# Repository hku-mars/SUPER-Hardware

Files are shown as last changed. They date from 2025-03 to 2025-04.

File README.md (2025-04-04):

# SUPER-Hardware

This repository contains the hardware components of the SUPER project. See the software part of SUPER at [hku-mars/SUPER (github.com)](https://github.com/hku-mars/SUPER)

If the following resources is useful to you, please cite our paper with

```bibtex
@article{ren2025safety,
  title={Safety-assured high-speed navigation for MAVs},
  author={Ren, Yunfan and Zhu, Fangcheng and Lu, Guozheng and Cai, Yixi and Yin, Longji and Kong, Fanze and Lin, Jiarong and Chen, Nan and Zhang, Fu},
  journal={Science Robotics},
  volume={10},
  number={98},
  pages={eado6187},
  year={2025},
  publisher={American Association for the Advancement of Science}
}
```

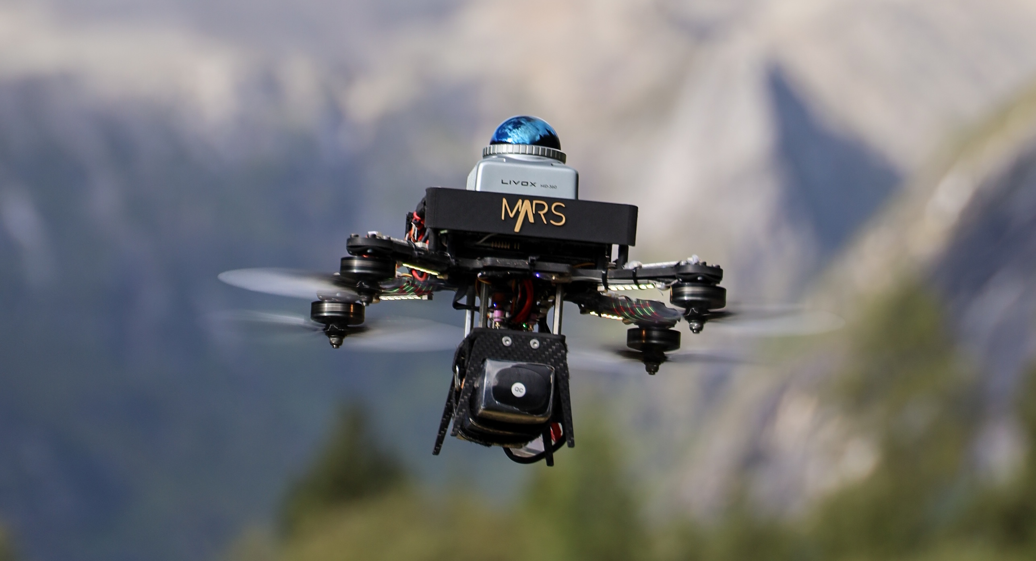
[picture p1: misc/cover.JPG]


## Provided Materials

We provide the following resources:

* Editable drafts and assemblies in SolidWorks: [./SolidWorks](./SolidWorks)
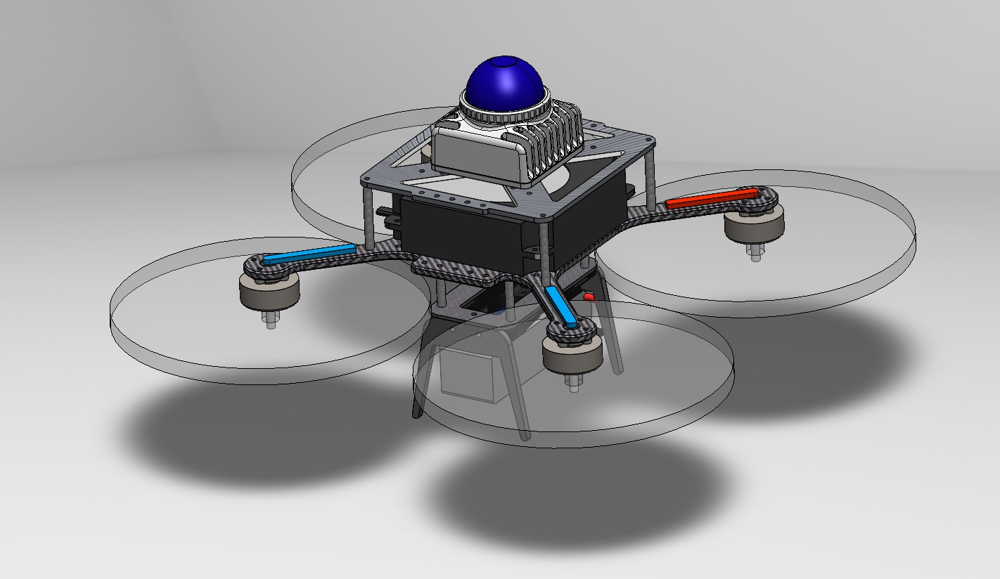
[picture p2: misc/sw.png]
  * 

* `.step` files for 3D printing: [./3DPrinting](./3DPrinting)

* `.step` files for carbon fiber cutting and engraving: [./CarbonFiber](./CarbonFiber)

Bill of Materials (BOM) for additional components with reference links (see table below)

## Hardware Breakdown

The hardware structure is illustrated below:

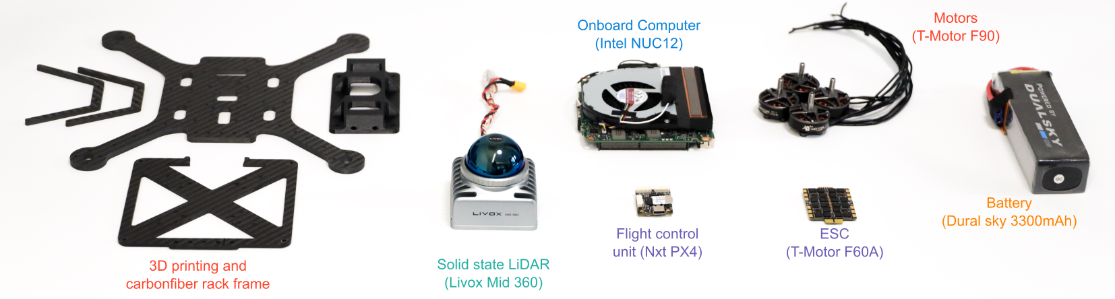
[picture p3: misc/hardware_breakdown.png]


## BOM

| Name | Type | Number | Reference Link |
| --- | --- | --- | --- |
| LiDAR | Livox MID360 | 1 | [Livox Mid-360 (livoxtech.com)](https://www.livoxtech.com/mid-360) |
| LiDAR Connecting Cable | N/A | 1 | [无名创新 Livox M12航插一分二数据线 mid360数据线 电赛无人机-淘宝网 (taobao.com)](https://item.taobao.com/item.htm?id=841090466365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{"aplus_abtest"%3A"eb7d480f961652917f78181296850d29"}&xxc=taobaoSearch) |
| Onboard Computer | Intel NUC | 1 | [ASUS NUC 12 Pro｜NUCs｜ASUS Global](https://www.asus.com/displays-desktops/nucs/nuc-kits/asus-nuc-12-pro/) |
| Aluminum Standoffs Pillars | 40 mm * 3 mm | 4 | |
| Aluminum Standoffs Pillars | 30 mm * 3 mm | 4 | (Or 8 pcs 40 mm * 3mm) |
| Motor | T-Motor F90 KV1300 | 4 | [T-MOTORHOBBY F90 2806.5 Long Range Motor - 1300KV/1500KV/1950KV_Motor_F Series Racing Power_FPV Drone Parts_Tmotorhobby Store-Tmotorobby drone motor,ESC,Propeller](https://tmotorhobby.com/goods.php?id=1057) |
| Propeller | HQ 7x4x3 | 4 | [HQProp 7X4X3 Light Grey](https://www.hqprop.com/hq-durable-prop-7x4x3-light-grey-2cw2ccw-poly-carbonate-popo-p0133.html)|
| ESC | T-Motor F60A mini 4 in 1 | 1 | [TMOTOR F60A MINI 20x20 4IN1 ESC for FPV Drones – T-Motor](https://shop.tmotor.com/products/f60a-mini-20x20-4in1-esc) |
| Battery | DualSky 3300mAh 6S XP-3300HED | 1 | [cn.dualsky.com/Xpower_LiPos/decc7a90-6c8f-5c0d-d0d4-c8eaced6f5d2.shtml](http://cn.dualsky.com/Xpower_LiPos/decc7a90-6c8f-5c0d-d0d4-c8eaced6f5d2.shtml) |
| Flight Controller | NxtPx4 | 1 | [NxtPX4v2(micoair.cn)](https://micoair.cn/docs/NxtPX4v2-fei-kong-yong-hu-shou-ce) |
| RC | Radiolink AT9S | 1 | [AT9S PRO 12 channels transmitter for racing drone, fixed wing, helicopter, glider, cars and boats (radiolink.com.cn)](https://www.radiolink.com.cn/at9spro) |
| Reveiver | Radiolink R12DSM | 1 | [12 channels MINI receiver R12DSM (radiolink.com)](https://www.radiolink.com/r12dsm) |
| Power Module | CKCS CK2416 (12 V 16 A)  | 1 | [https://e.tb.cn/h.6U3o07BuE81jHGi?tk=fopteCChcyW](https://e.tb.cn/h.6U3o07BuE81jHGi?tk=fopteCChcyW) |
### Notes:

- **RC and Receiver**: The listed models (Radiolink AT9S and R12DSM) are what we currently use, but alternatives are acceptable.

- **Battery**: Any 6S battery can be used, not necessarily the DualSky model listed.

- **Flight Controller**: Any PX4-compatible flight controller can substitute for the NxtPx4, as the MPC controller may be open-sourced later this year, and our development is based on PX4.

- **Power module for NUC**: We are currently using a customized DC-DC buck converter designed by a labmate, but we do not have plans to make it open-source at this time. However, you may find the following open-source option useful: [NUC Battery Power - Open Source Hardware Platform.](https://oshwhub.com/PancLAN/buck_for_nuc). Please note that this open-source solution is not very stable, which is why we are making some modifications. However, these updates are not being handled by me, so I don't have further details. We may provide updates in the future.

  **UPDATE 24/04/04:** I have found an alternative for NUC 13 or other types that supports 12 v inputs, listed in the table above.

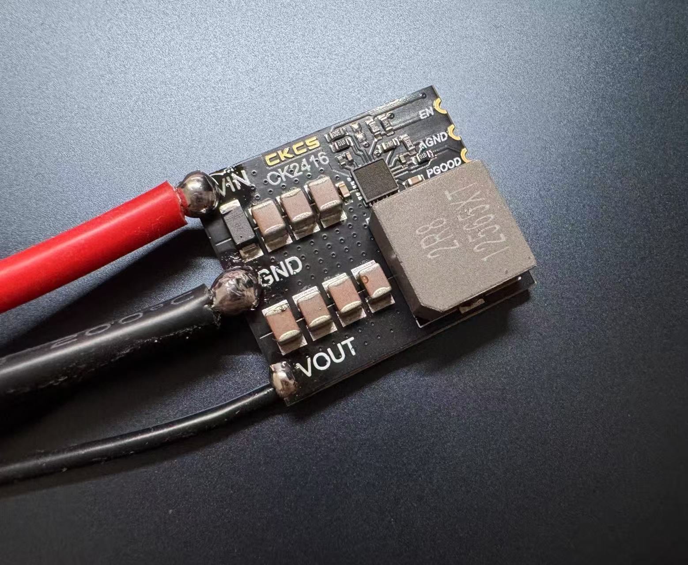
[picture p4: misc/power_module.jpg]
  

## Acknowledgments

- Special thanks to [NxtPx4](https://github.com/HKUST-Aerial-Robotics/Nxt-FC) for providing an excellent mini flight controller.
- Gratitude to all contributors: **Wenyi Liu**, **Wendi Dong**, **Minghe Chen**, and **Rongpei Dai**.

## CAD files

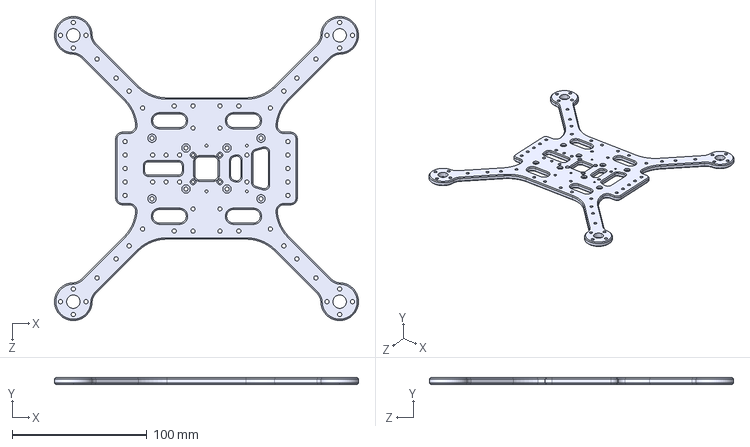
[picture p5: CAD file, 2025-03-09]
CarbonFiber/5mm_main_board.STEP
226.0 x 5.00 x 226.0 mm

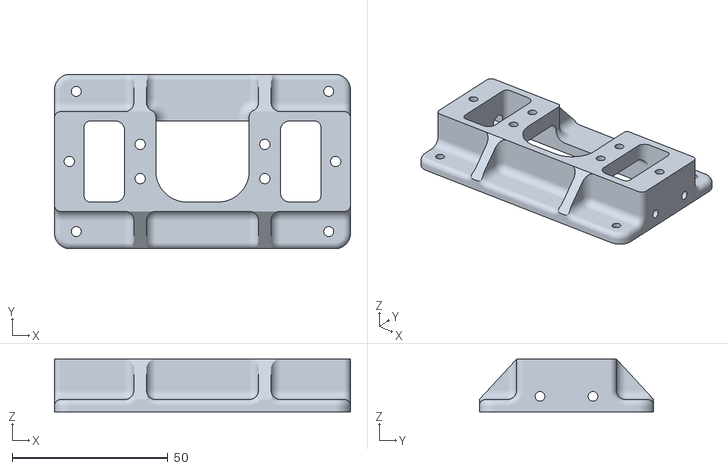
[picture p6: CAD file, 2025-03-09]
3DPriting/battery_board.stl
95.0 x 56.0 x 17.0

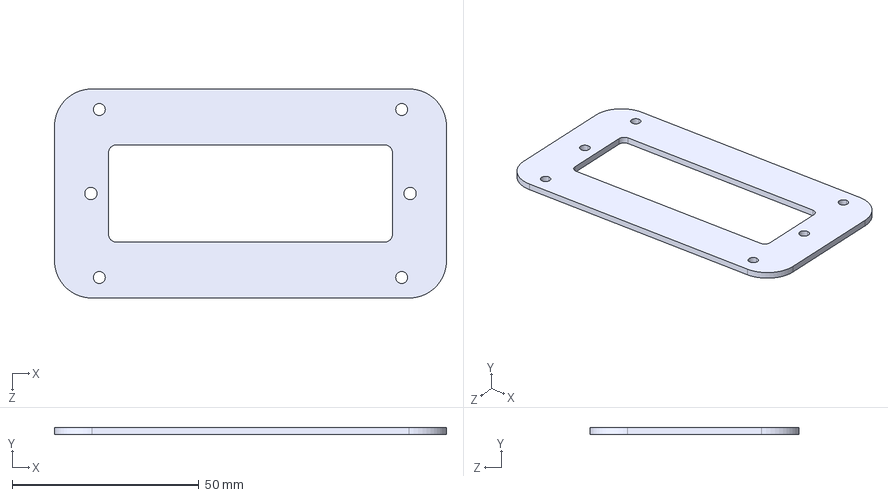
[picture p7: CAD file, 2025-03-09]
CarbonFiber/3mm_bat_board.step
105.0 x 2.00 x 56.0 mm

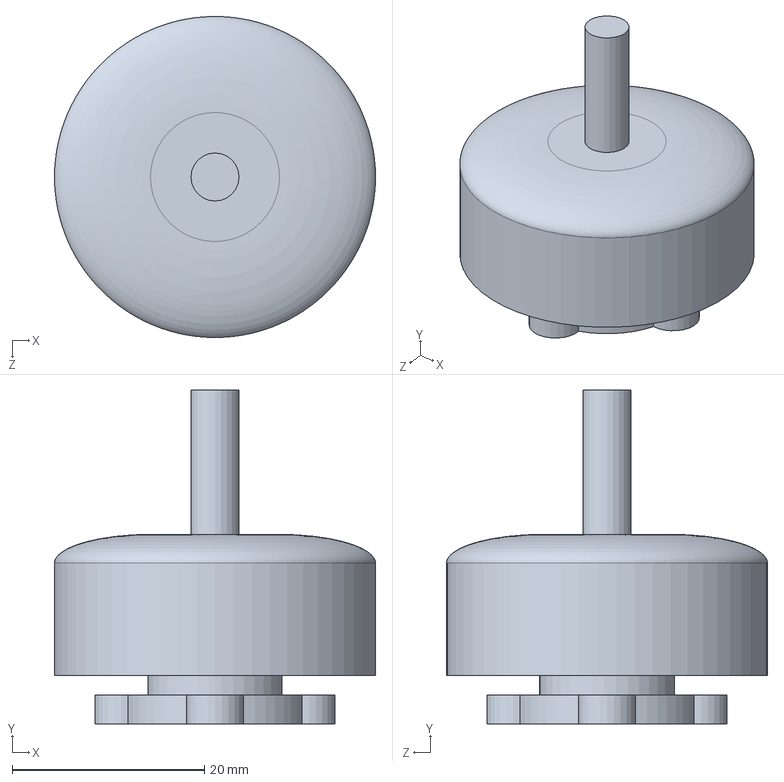
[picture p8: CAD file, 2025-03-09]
SolidWorks/yunque-F90_motor.SLDPRT
33.4 x 34.7 x 33.4 mm

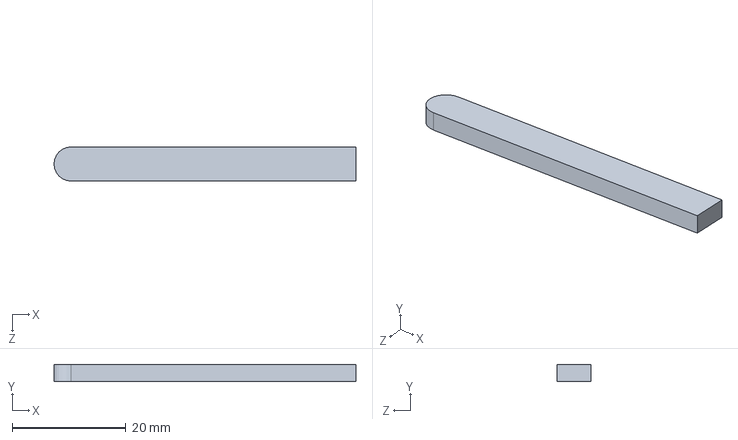
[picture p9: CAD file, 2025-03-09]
SolidWorks/yunque-led-b.SLDPRT
53.0 x 3.00 x 6.00 mm

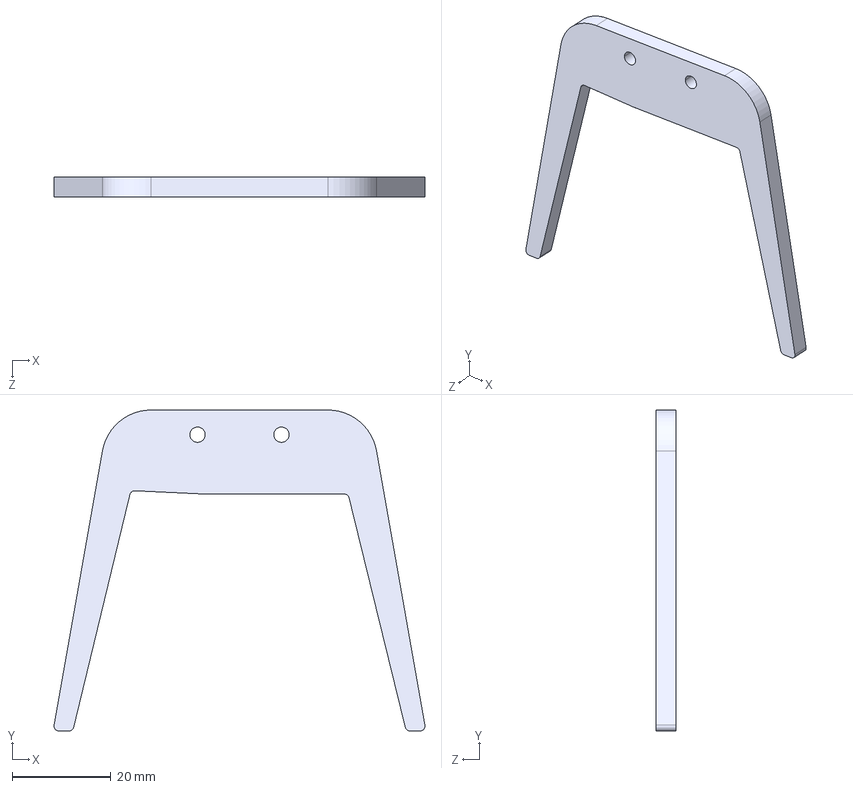
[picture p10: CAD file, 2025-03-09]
CarbonFiber/4mm-foot.STEP
75.1 x 65.0 x 4.00 mm

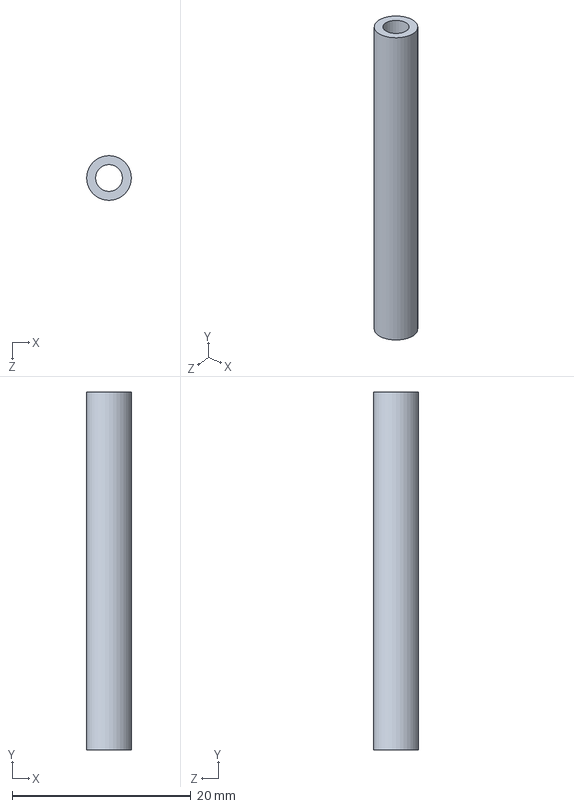
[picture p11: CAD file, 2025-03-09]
SolidWorks/40mm_alu_pillar.SLDPRT
5.00 x 40.0 x 5.00 mm

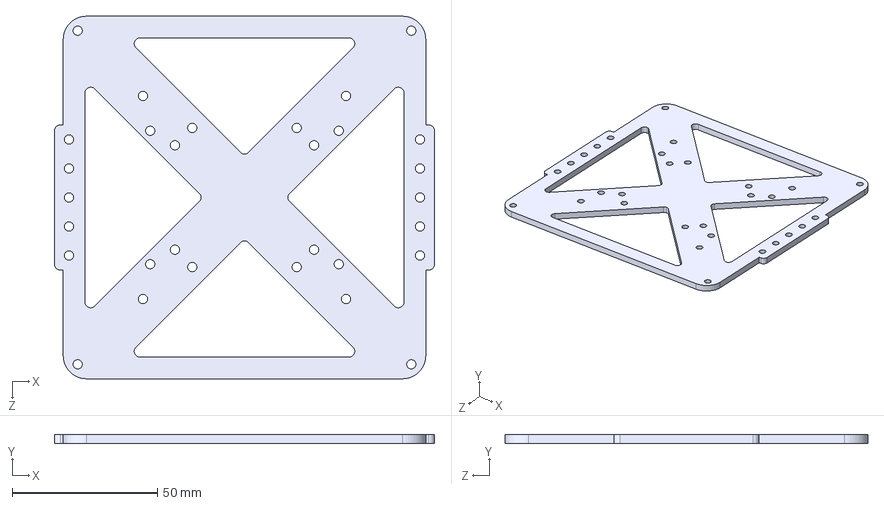
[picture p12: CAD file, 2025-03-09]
CarbonFiber/3mm_sec_board.step
131.0 x 3.00 x 125.0 mm

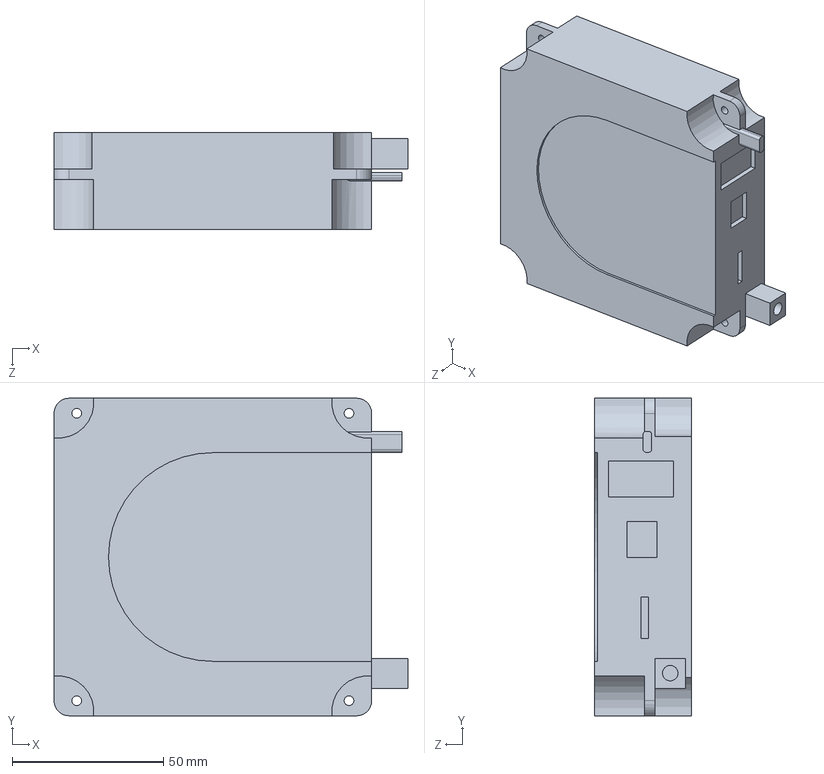
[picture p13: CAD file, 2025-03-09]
SolidWorks/yunque-intel_nuc.SLDPRT
117.0 x 105.0 x 32.0 mm

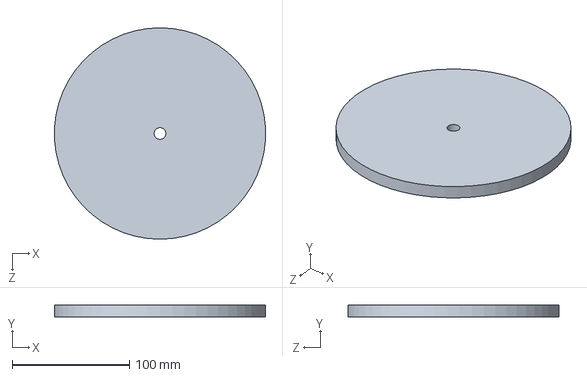
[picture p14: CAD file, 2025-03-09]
SolidWorks/yunque-prop.SLDPRT
179.7 x 10.0 x 180.0 mm

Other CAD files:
SolidWorks/yunque-mainboard.SLDPRT
SolidWorks/yunque_bat_board.SLDPRT
SolidWorks/yunque-led-a.SLDPRT
SolidWorks/battery_board-STL1.SLDPRT
SolidWorks/yunque-battery_board.SLDPRT
SolidWorks/landing_board.SLDPRT
SolidWorks/yunque-foot-4mm.SLDPRT
SolidWorks/battery_board-STL.SLDPRT
SolidWorks/30mm_alu_pillar.SLDPRT
SolidWorks/battery_board-STL.stl
SolidWorks/yunque-LiDARboard.SLDPRT
SolidWorks/yunque-dualsky-bat.SLDPRT

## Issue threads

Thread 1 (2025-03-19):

Does NUC's Power Supply Require a Voltage Regulator Module?

Joosoo1, 2025-03-19:
I understand that the input voltage range for NUC is 12-19V, while the output voltage of a 6S lithium battery ranges from 22.2V to 25.2V. Using a 6S battery seems to require a step-down module, but the step-down modules that meet NUC's power requirements are quite large in size. Have you used any step-down modules? If so, could you recommend one to me? Thank you very much!

RENyunfan, 2025-03-19:
That's a great question! We currently use a customized DC-DC buck converter designed by a labmate, but we don't have plans to make it open-source at this time. However, you might find the following open-source option useful: https://oshwhub.com/PancLAN/buck_for_nuc

RENyunfan, 2025-03-28:
Please note that this open-source solution is not very stable, which is why we are making some modifications. However, these updates are not being handled by me, so I don't have further details. We may provide updates in the future.

Closed 2025-03-19.

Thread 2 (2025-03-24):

硬件结构相关示意图

yeyuqing2950, 2025-03-24:
尊敬的开发团队，您好，我是来自福建的一个物联网爱好者，最近对飞行器这块想要有更深入了解，无意间看到此项目，对项目的兴趣很浓厚，想自己复现，购买配件后想要一份相关硬件示意图，因为我对一些控制板安装的位置无法确定，担心在起飞后出现很多意外故障，因此想参考你们的安装方式，减少损失；很感谢你们能看到这个issues，期待你们的回复。

RENyunfan, 2025-03-27:
感谢您的关注，我们的飞控和电调以飞塔的形式安装在机身中间20*20mm的孔位上。其他的安装没有什么特别需要注意的。NUC的供电需要一个高性能的buck，我们使用的是内部设计的一个模块。如果需要替代品，可以参考https://oshwhub.com/PancLAN/buck_for_nuc

Closed 2025-03-27.

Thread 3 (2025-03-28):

How does NUC get the 20V power?

chenfch3, 2025-03-28:
[https://github.com/hku-mars/SUPER/issues/5#issuecomment-2758276567](url)

RENyunfan, 2025-03-28:
That's a great question! We currently use a customized DC-DC buck converter designed by a labmate, but we don't have plans to make it open-source at this time. However, you might find the following open-source option useful: https://oshwhub.com/PancLAN/buck_for_nuc. I will update this information to README.md

RENyunfan, 2025-03-28:
Please note that this open-source solution is not very stable, which is why we are making some modifications. However, these updates are not being handled by me, so I don't have further details. We may provide updates in the future.

Closed 2025-03-28.

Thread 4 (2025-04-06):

General questions about the hardware

Emerlads, 2025-04-06:
•	What frequency band was used for the Radiolink AT9S Pro and R12DSM receiver?
	•	Were there any signal interference or range issues during testing?
	•	Would you recommend modifying the antenna setup for improved signal reliability in field operations?

	•	Based on your flight tests, what was the real-world battery life of the 6S 3300mAh LiPo?
	•	Did you find the 70C discharge rate sufficient, or would a higher/lower C rating provide better performance?
	•	Were any additional power management strategies (e.g., secondary regulators, power filtering) used to optimize efficiency?

	•	We are using an NVIDIA Jetson Orin Mini instead of the Intel NUC used in the original SUPER drone.
	•	Did you find any CPU/GPU bottlenecks with the NUC that might indicate whether the Orin Mini is a better fit?
	•	Were there any specific PX4 configurations or LiDAR processing methods that relied on x86 architecture, which might require adjustments for ARM-based Jetson?
	•	The carbon fiber frame presents challenges in manufacturing and precision cutting.

	•	Was there specific post-processing or filtering applied in software to handle environmental interference (e.g., reflections, motion blur, or sensor drift)?

RENyunfan, 2025-04-23:
**1. What frequency band was used for the Radiolink AT9S Pro and R12DSM receiver?**

The AT9S Pro and R12DSM use the 2.4 GHz band.

**2. Were there any signal interference or range issues during testing?**

No, tests in a dense forest showed minimal signal interference.

**3. Would you recommend modifying the antenna setup for improved signal reliability in field operations?**

No modifications were made or deemed necessary.

**4. Based on your flight tests, what was the real-world battery life of the 6S 3300mAh LiPo?**

Approximately 12 minutes.

**5. Did you find the 70C discharge rate sufficient, or would a higher/lower C rating provide better performance?**

The 70C rate was sufficient; lower rates may work, but weren’t tested.

**6. Were any additional power management strategies (e.g., secondary regulators, power filtering) used to optimize efficiency?**

We used a TVS diode to prevent power-on surges and a 1000µF capacitor to stabilize back-EMF disturbances.

**7. We are using an NVIDIA Jetson Orin Mini instead of the Intel NUC used in the original SUPER drone. Is this okay?**

Yes, no issues with the Jetson Orin Mini.

**8. Did you find any CPU/GPU bottlenecks with the NUC that might indicate whether the Orin Mini is a better fit?**

We only used the CPU. Tests with Jetson NX showed no issues, suggesting the Orin Mini should work well.

**9. Were there any specific PX4 configurations or LiDAR processing methods that relied on x86 architecture, which might require adjustments for ARM-based Jetson?**

No, PX4 and LiDAR processing are compatible with ARM architecture.

**10. The carbon fiber frame presents challenges in manufacturing and precision cutting. Any concerns?**

The 3D structure is optional but beneficial. You can remove it from the sw files if needed.

**11. Was there specific post-processing or filtering applied in software to handle environmental interference (e.g., reflections, motion blur, or sensor drift)?**

Our FAST-LIO algorithm is robust enough; no additional post-processing was needed.

Closed 2025-04-23.

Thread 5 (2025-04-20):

Request for PID tuning parameters

Coder0551, 2025-04-20:
Hi, thanks for your share! I have successfully assembled the drone according to the BOM instructions, using components that exactly match the specifications. The aircraft can take off, but is somewhat difficult to control. Could you please provide us with the relevant PID parameters? We're using QGC as our ground station software. Looking forward to your reply. Thank you!

RENyunfan, 2025-04-23:
Sure, we use the Generic 250 Racer airframe. The key is to lower the D-term to minimize vibrations.

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

Coder0551, 2025-04-29:
Thanks! After implementing your suggestions, the drone's attitude stability has improved significantly！

Closed 2025-04-23.

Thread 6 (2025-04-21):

Does MID360 need additional vibration reduction?

XXLiu-HNU, 2025-04-21:
Thanks to the author for open source.

 We re-assembled a quadcopter with reference to your hardware, but in actual use, we found that the MID360's imu vibration changed greatly after the drone started to take off, causing the LIO algorithm to fail.

We first manually moved the drone to ensure the LIO algorithm was working properly, then used the remote controller to unlock the drone and gave it some throttle. After the drone took off, LIO began to drift.

The following three pictures show the data of mid360 imu at the beginning of takeoff, the positioning of fastlio2 and our drone hardware. We only added a d435i camera in the front, and the rest is similar to your hardware.

Do we need to consider adding shock absorption to mid360 during the design?

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

RENyunfan, 2025-04-23:
Great question! We recommend using the IMU within the FCU, as it’s more robust against vibrations. Ensure you calibrate the spatial-temporal extrinsics with tools like https://github.com/hku-mars/LiDAR_IMU_Init.

Closed 2025-04-23.

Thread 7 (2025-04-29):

Flight Performance Issues After Assembly

Coder0551, 2025-04-29:
Thank you for your guidance!  I’ve successfully assembled the drone following the BOM instructions and tuned the PID parameters to match your provided values. The drone can take off, but I’m encountering two key issues:

  1. Short Flight Time (<3 mins)  : After adding the LiDAR and onboard computer, the drone’s weight seems excessive, drastically reducing flight time, with our actual measured flight time being less than 3 minutes.
  2. Besides LiDAR, do you suggest integrating other sensors (e.g., optical flow, GPS) to enhance positioning stability? If so, could you share any tested configurations or tips?

Looking forward to your reply!

RENyunfan, 2025-04-29:
The supplementary materials for your paper demonstrate that the system's endurance exceeds 10 minutes, as shown in this video: [YouTube Link](https://www.youtube.com/watch?v=4QKODwLw4ao&ab_channel=MARSLABHKU). However, I'm unsure why your system has a battery life of less than 3 minutes.

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

Additionally, we did not use other sensors in our tests, as the LiDAR-IMU odometry proved more robust and accurate than GPS or optical flow. However, incorporating GPS as a backup for outdoor scenarios could be beneficial.

Coder0551, 2025-05-13:
Problem solved! The drone’s battery drained too fast because the propellers were put on backwards, so it couldn’t generate enough lift.

RENyunfan, 2025-05-14:
> Problem solved! The drone’s battery drained too fast because the propellers were put on backwards, so it couldn’t generate enough lift. The system now achieves an endurance exceeding 20 minutes under no-load conditions.

Great to hear—best of luck with your future endeavors.

Closed 2025-04-29.

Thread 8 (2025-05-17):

Can you share the firmware and parameter files used in your experiment for NxtPX4 V2?

Joosoo1, 2025-05-17:
Thank you for open-sourcing your project. After setting up the drone based on the "SUPER-Hardware" configuration, I frequently encounter yaw estimation errors. I suspect interference with my external magnetometer. Could you confirm whether you disabled the external magnetometer during your 'SUPER' testing?

Additionally, have you tested px4ctrl for trajectory tracking? If so, would you be able to share the PID parameters?

Closed 2025-05-22.

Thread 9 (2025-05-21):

遇到机架共振的问题

yeyuqing2950, 2025-05-21:
亲爱的创作团队：
        您好！我已经将材料买齐，并且组装成功，但是在试飞时有遇到机架共振的问题，将螺旋桨拆掉后放在平面上，开机试飞，机身有很大晃动，咨询身边的朋友后发现可能存在机架共振的问题，导致晃动较大，请问你们有遇到吗，如果有遇到的话，可以传授一下解决方案吗，很感谢您的回复。

yeyuqing2950, 2025-05-23:
很感谢您对我的回复，但是我目前在空中飞行时依然会出现自旋的情况，在加大油门后，机器会以一种螺旋式的姿态往上飞行，将机器螺旋桨拆下后，平稳放置，无人机晃动很大，电机噪声很大；但倾斜一定角度后无人机的电机旋转就会变得匀速，声音稳定；已经参考(https://github.com/hku-mars/SUPER-Hardware/issues/5）中的参数信息进行调试后，依然会出现上面的症状，目前也无法找到原因；请问你们有遇到相似的故障吗

yeyuqing2950, 2025-05-23:
嗯嗯 谢谢您对我的回复 我这边再自己排查一下看看 很感谢您对我的回答

Closed 2025-05-23.

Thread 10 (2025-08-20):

Looking for 3D diagram for the propellor guards

RizviRaza, 2025-08-20:
I just saw the video "Nature Communications: Slope Inspection under Dense Vegetation Using LiDAR-based Quadrotors", which uses the SUPER drone as the platform.

I am looking for the printable 3D model of propeller guards installed on the SUEPR drone, as shown in the video.

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

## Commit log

2025-03-09 first submit
    [30mm_alu_pillar.SLDPRT, 3mm_bat_board.step, 3mm_sec_board.step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]
2025-03-27 Update README.md
    add propeller
2025-04-04 update power module
